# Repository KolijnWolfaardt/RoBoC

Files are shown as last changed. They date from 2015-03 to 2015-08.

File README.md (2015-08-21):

# RoBoC
The RoBoC is a robotics controller board designed for the Robotics club of Stellenbosch. It features a dsPIC33 microcontroller, a motor river and plenty of IO pins. This was designed to be cheaper than off the shelf development boards with the necessary extras.

Please see the full documentation at [http://kolijnwolfaardt.github.io/RoBoC/](http://kolijnwolfaardt.github.io/RoBoC/)

# About the PCB Design
The PCB is designed in [Kicad](www.kicad-pcb.org/). All the project files can be found in *./PCB Design*, and the extra component footprints created are in *./PCB Design/lib*. Some of these components are adapted from the libraries supplied with KiCad. 

The board was originally designed as a 4 layer board, with power and some signals on the inner copper layers. This proved to be too expensive, so the board was redesigned as a 2-layer board.

# Bootloader
## ds30 Bootloader
The ds30 Bootloader code supplied here is a modified version of the [ds30 Loader](http://picbootloader.com/). The following changes were made:

 - The initialization includes configuring the oscillator and PLL
 - The UART initialization was simplified.
 - An LED on the board is turne on and off to indicate when the bootloader is waiting for commands.
 - The memory footprint of the bootloader was reduces by commenting out some of the original (unused) code.

### Compiling the Bootloader
To compile the bootloader the MPLAB IDE v8.92 and the ASM30 compiler were used, on a pc running Windows. The resulting hex file can be written to the board using a PicKit2 or PicKit3.

### Using the Bootloader
To use the bootloader, use the program supplied on the ds30 Loader website.

# Technical Details
 - The Microcontroller is a [dsPic33FJ32GS606](http://www.microchip.com/wwwproducts/Devices.aspx?dDocName=en546851)
 - USB to UART IC is a [MCP2200](http://www.microchip.com/wwwproducts/devices.aspx?dDocName=en546923)
 - The Motor driver is a ON Semiconductor [LV8405V](http://www.onsemi.com/PowerSolutions/product.do?id=LV8405V)
 - The PCB is a 2-layer 5cm by 10cm board

# License
 - The Hardware is licensed under the [CERN OSH License ](http://www.ohwr.org/attachments/2388/cern_ohl_v_1_2.txt)
 - The ds30 Bootloader is licensed under the [GNU GPLv2 Licens](http://www.gnu.org/licenses/old-licenses/gpl-2.0.en.html)
 - Software written for the board is licensed under the [CC Attribution-NonCommerical License ](https://creativecommons.org/licenses/by-nc/2.0/legalcode)

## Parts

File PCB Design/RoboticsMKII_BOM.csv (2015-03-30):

C1 | 1uF | Capacitors_SMD:C_1206
C2 | 100nF | Capacitors_SMD:C_1206
C3 | 1uF | Capacitors_SMD:C_1206
C4 | 1uF | Capacitors_SMD:C_1206
C5 | 100nF | Capacitors_SMD:C_1206
C6 | 100nF | Capacitors_SMD:C_1206
C7 | 100nF | Capacitors_SMD:C_1206
C8 | 100nF | Capacitors_SMD:C_1206
C9 | 100nF | Capacitors_SMD:C_1206
C10 | 10nF | Capacitors_SMD:C_1206
C11 | 100nF | Capacitors_SMD:C_1206
C12 | 10nF | Capacitors_SMD:C_1206
C13 | 10nF | Capacitors_SMD:C_1206
C14 | 10nF | Capacitors_SMD:C_1206
C15 | 22pF | Capacitors_SMD:C_1206
C16 | 22pF | Capacitors_SMD:C_1206
C17 | 100nF | Capacitors_SMD:C_1206
C18 | 22pF | Capacitors_SMD:C_1206
C19 | 22pF | Capacitors_SMD:C_1206
C20 | 10uF | Capacitors_SMD:C_1206
C21 | 100nF | Capacitors_SMD:C_1206
C22 | 10uF | Capacitors_SMD:C_1206
C23 | 1uF | Capacitors_SMD:C_1206
R1 | 220 | Resistors_SMD:R_1206
R2 | 4.7k | Resistors_SMD:R_1206
R3 | 220 | Resistors_SMD:R_1206
R4 | 220 | Resistors_SMD:R_1206
R5 | 220 | Resistors_SMD:R_1206
R6 | 220 | Resistors_SMD:R_1206
R7 | 4.7k | Resistors_SMD:R_1206
R8 | 220 | Resistors_SMD:R_1206
R9 | 4.7k | Resistors_SMD:R_1206
R11 | 220 | Resistors_SMD:R_1206
R12 | 220 | Resistors_SMD:R_1206
R10 | 18k | Resistors_SMD:R_1206
R13 | 220 | Resistors_SMD:R_1206
R14 | 4.7k | Resistors_SMD:R_1206
F1 | FUSE
D1 | LED | LEDs:LED-1206
D2 | LED | LEDs:LED-1206
D3 | LED | LEDs:LED-1206
D4 | LED | LEDs:LED-1206
D5 | LED | LEDs:LED-1206
D6 | LED | LEDs:LED-1206
D7 | LED | LEDs:LED-1206
D8 | LED | LEDs:LED-1206
D9 | D | Diode
RESET1 | DPST | Buttons_Switches_SMD:SW_SPST_PTS645
SW0 | DPST | Buttons_Switches_SMD:SW_SPST_PTS645
SW1 | DPST | Buttons_Switches_SMD:SW_SPST_PTS645
CON1 | USB-MICRO-B | USB
U1 | 3.3VREG
U2 | LV8405V
U3 | MCP2200
U4 | dsPIC33FJ32GS606 | TQFP
X1 | 12MHz
X2 | 10MHz
P1 | CONN_01X03 | Pin_Headers:Pin_Header_Straight_1x03
P2 | CONN_01X02
P3 | CONN_01X03 | Pin_Headers:Pin_Header_Straight_1x03
P4 | CONN_01X03 | Pin_Headers:Pin_Header_Straight_1x03
P5 | CONN_01X03 | Pin_Headers:Pin_Header_Straight_1x03
P6 | CONN_01X03 | Pin_Headers:Pin_Header_Straight_1x03
P7 | CONN_01X03 | Pin_Headers:Pin_Header_Straight_1x03
P8 | CONN_01X03 | Pin_Headers:Pin_Header_Straight_1x03
P9 | CONN_01X08 | Pin_Headers:Pin_Header_Straight_1x08
P10 | CONN_02X11 | Pin_Headers:Pin_Header_Straight_2x11
P11 | CONN_01X03 | Pin_Headers:Pin_Header_Straight_1x03
P12 | CONN_01X02 | Pin_Headers:Pin_Header_Straight_1x02
P13 | CONN_01X06 | Pin_Headers:Pin_Header_Straight_1x06
P14 | CONN_01X06 | Pin_Headers:Pin_Header_Straight_1x06

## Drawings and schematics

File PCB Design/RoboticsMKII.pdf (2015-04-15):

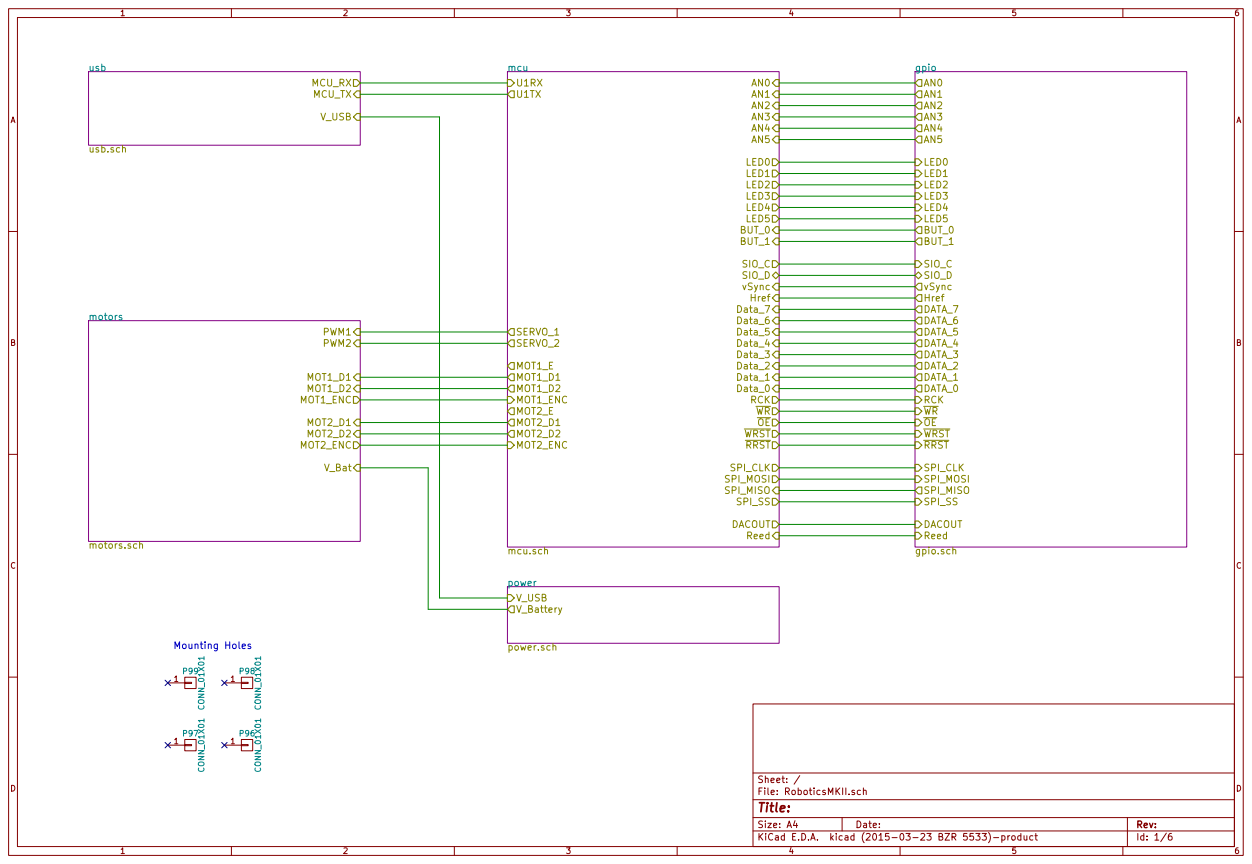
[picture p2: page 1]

Id: 1/6 Title: File: RoboticsMKII.sch Sheet: / power power.sch
V_USB

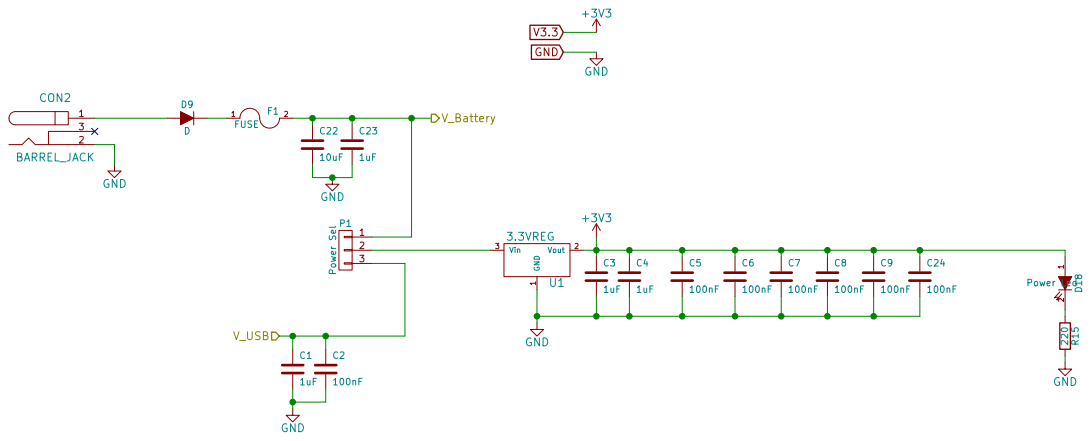
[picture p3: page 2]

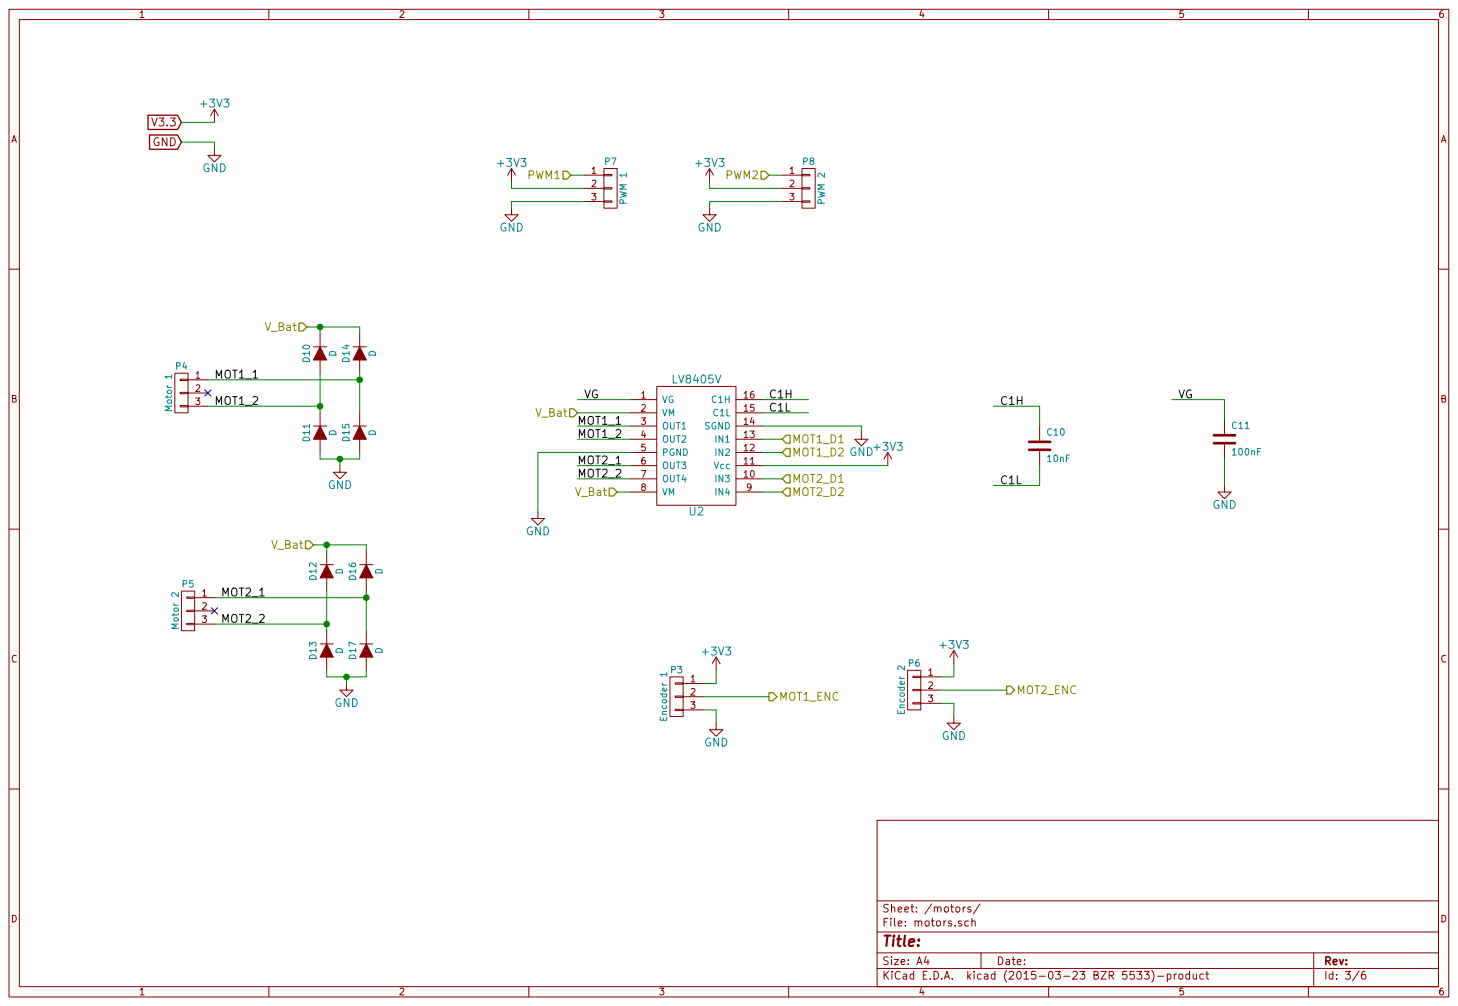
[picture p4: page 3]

Id: 3/6 Title: File: motors.sch Sheet: /motors/

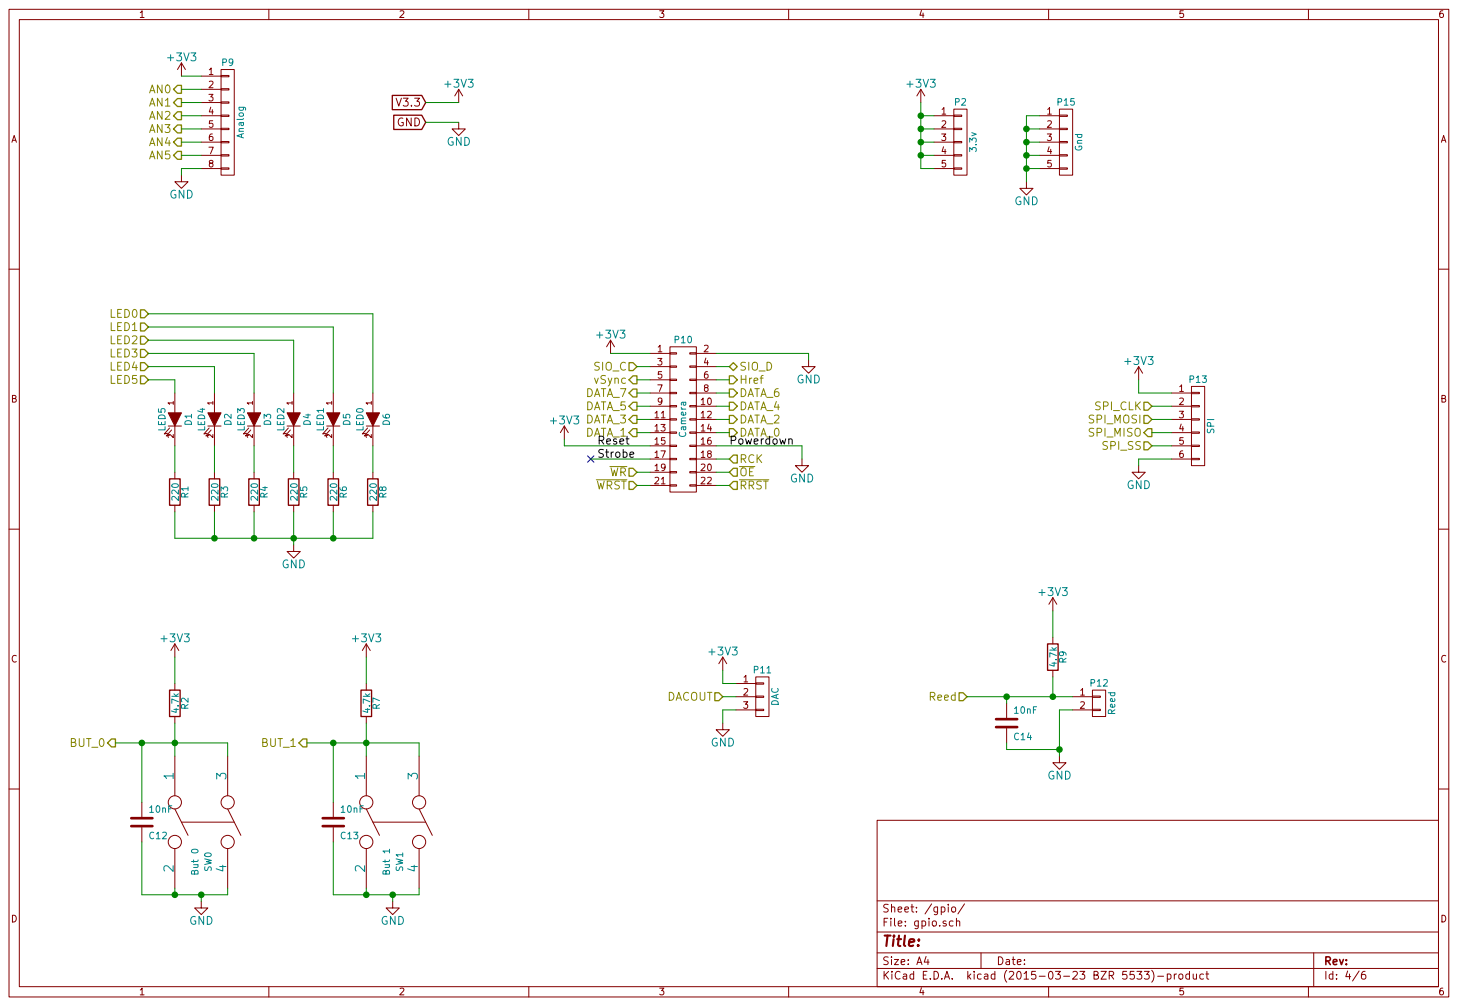
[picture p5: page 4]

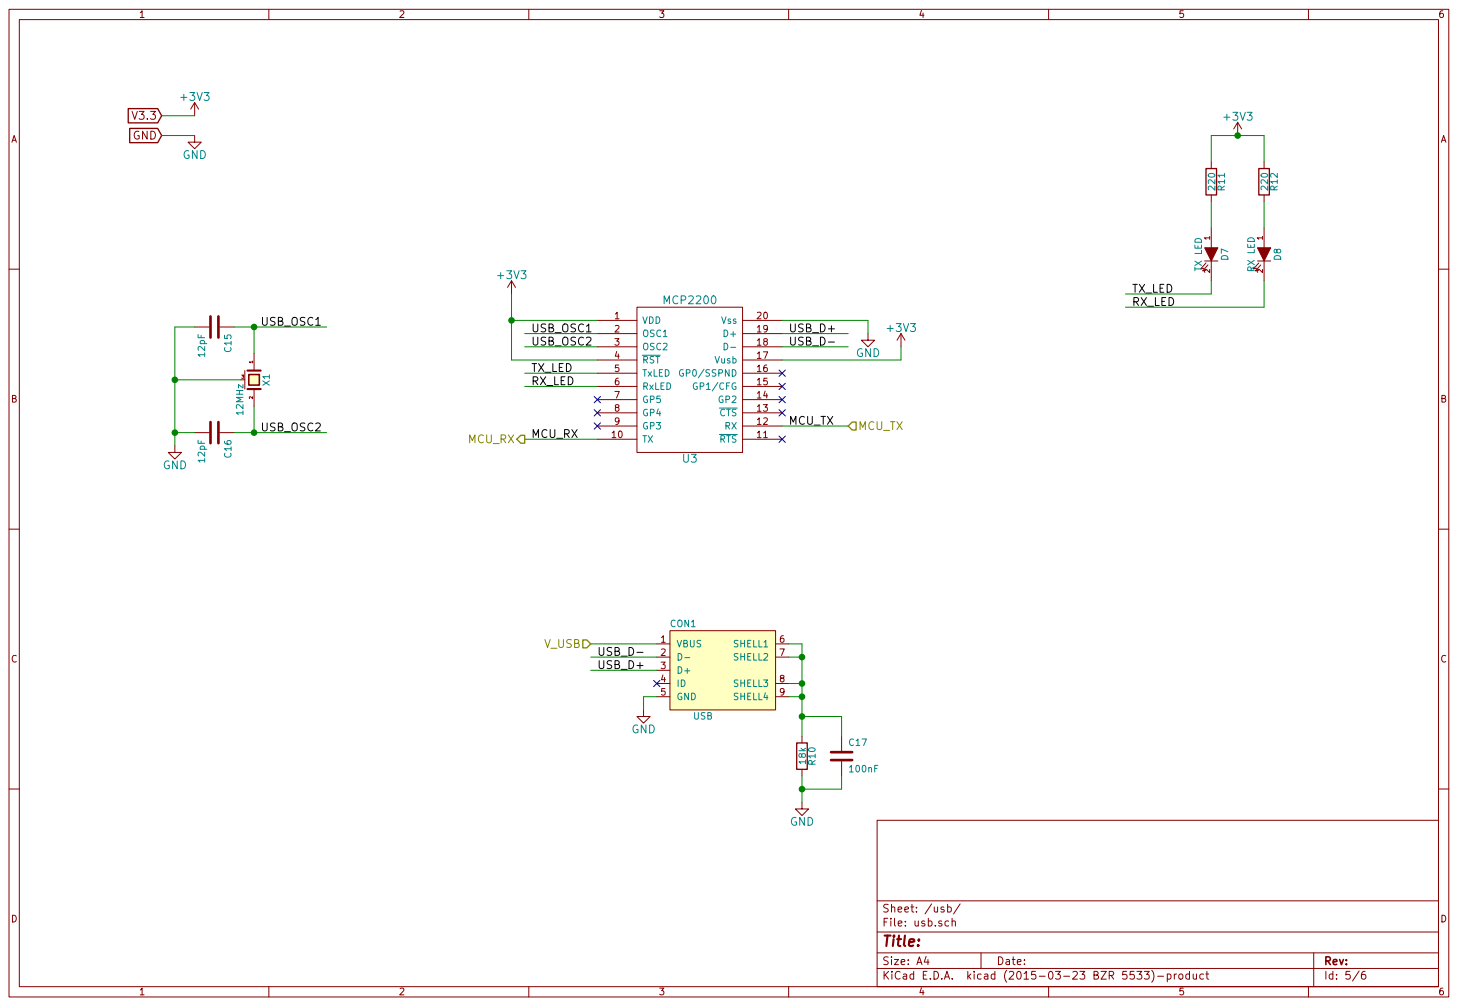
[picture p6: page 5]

Id: 5/6 Title: File: usb.sch Sheet: /usb/

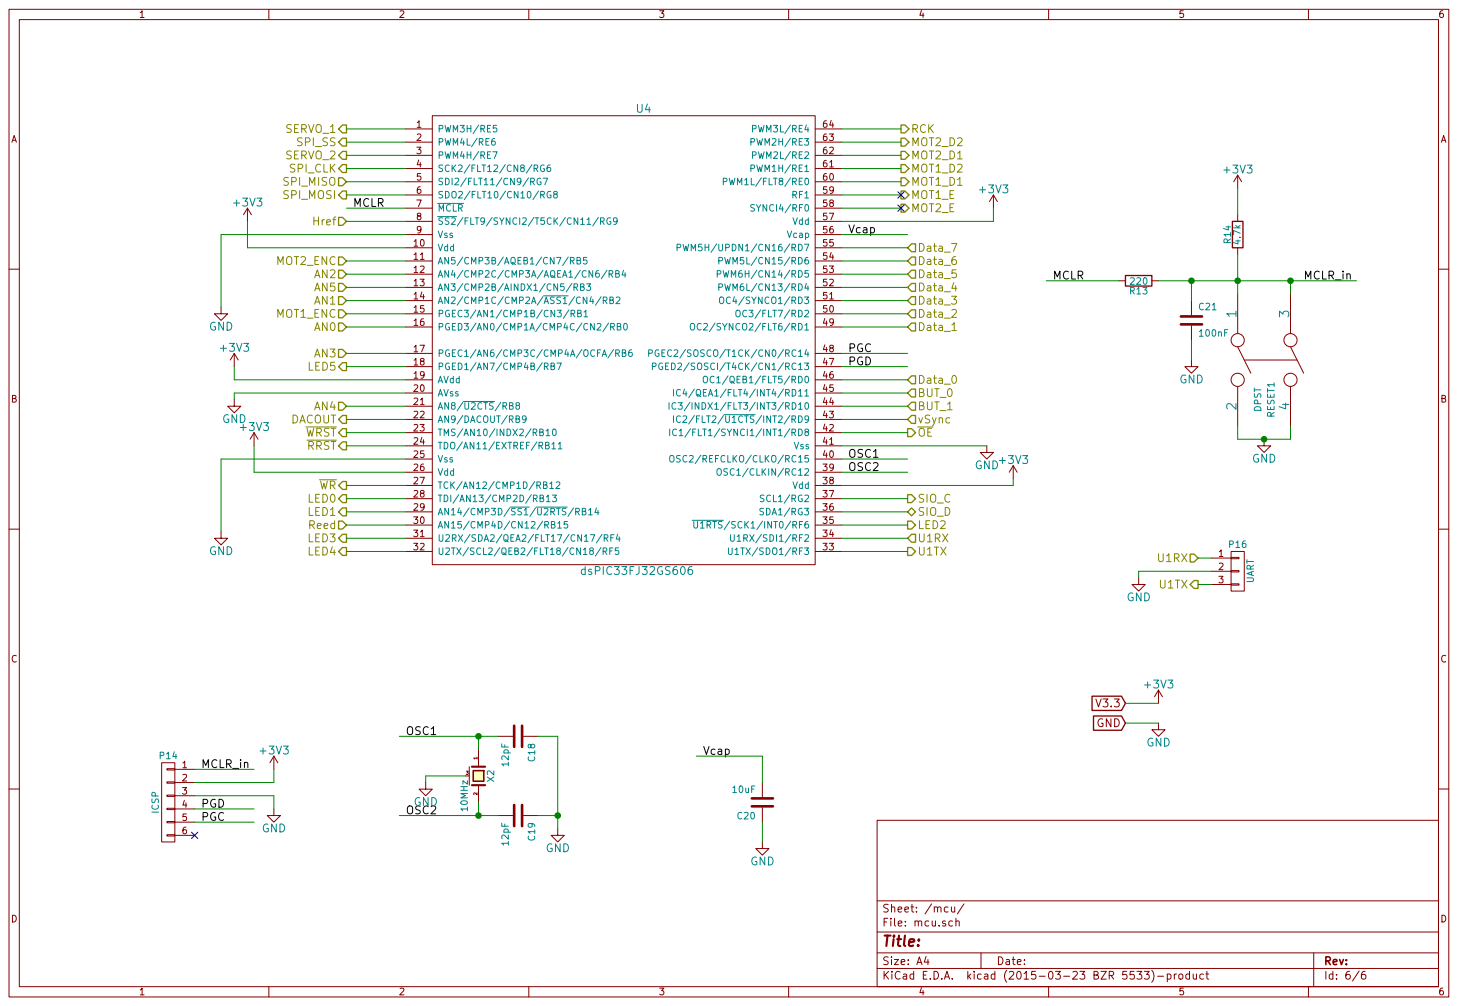
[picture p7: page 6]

Id: 6/6 Title: File: mcu.sch Sheet: /mcu/

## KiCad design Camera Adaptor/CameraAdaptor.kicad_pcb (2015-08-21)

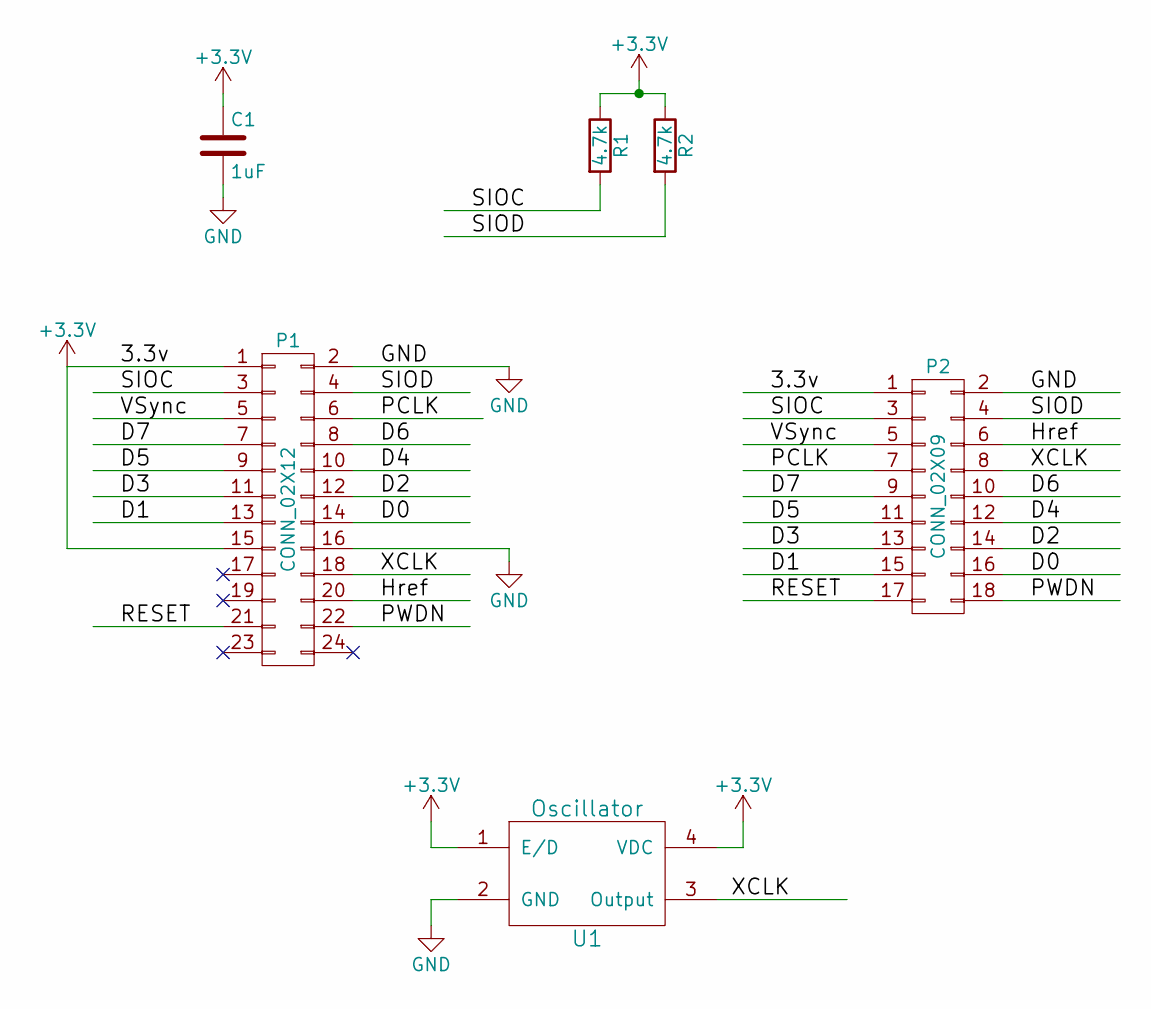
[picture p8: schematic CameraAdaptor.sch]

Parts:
C1: 1uF; C_1206_HandSoldering
P1: CONN_02X12; Pin_Header_Straight_2x12
P2: CONN_02X09; Pin_Header_Straight_2x09
R1, R2: 4.7k; R_1206_HandSoldering
U1: Oscillator; oscillator

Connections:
+3V3: C1.1, P1.1, P1.15, P2.1, R1.1, R2.1, U1.1 (E/D), U1.4 (VDC)
/D0: P1.14, P2.16
/D1: P1.13, P2.15
/D2: P1.12, P2.14
/D3: P1.11, P2.13
/D4: P1.10, P2.12
/D5: P1.9, P2.11
/D6: P1.8, P2.10
/D7: P1.7, P2.9
/Href: P1.20, P2.6
/PCLK: P1.6, P2.7
/PWDN: P1.22, P2.18
/RESET: P1.21, P2.17
/SIOC: P1.3, P2.3, R1.2
/SIOD: P1.4, P2.4, R2.2
/VSync: P1.5, P2.5
/XCLK: P1.18, P2.8, U1.3 (Output)
GND: C1.2, P1.2, P1.16, P2.2, U1.2 (GND)

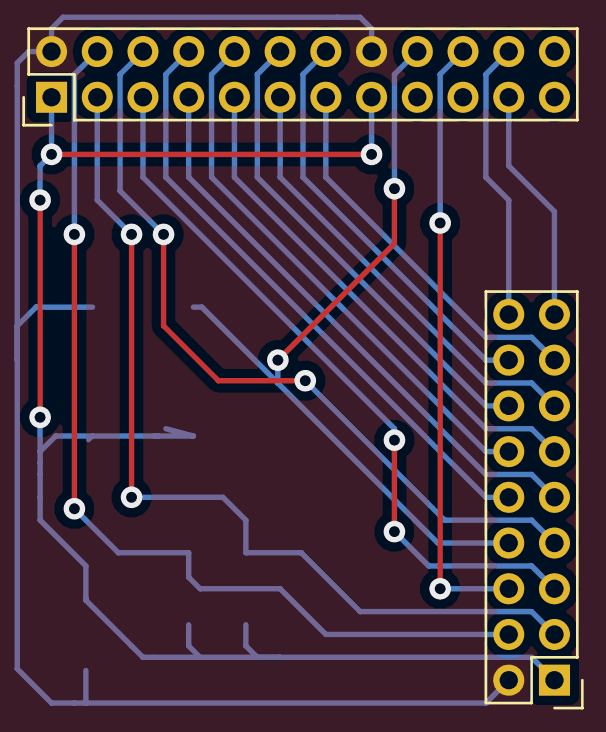
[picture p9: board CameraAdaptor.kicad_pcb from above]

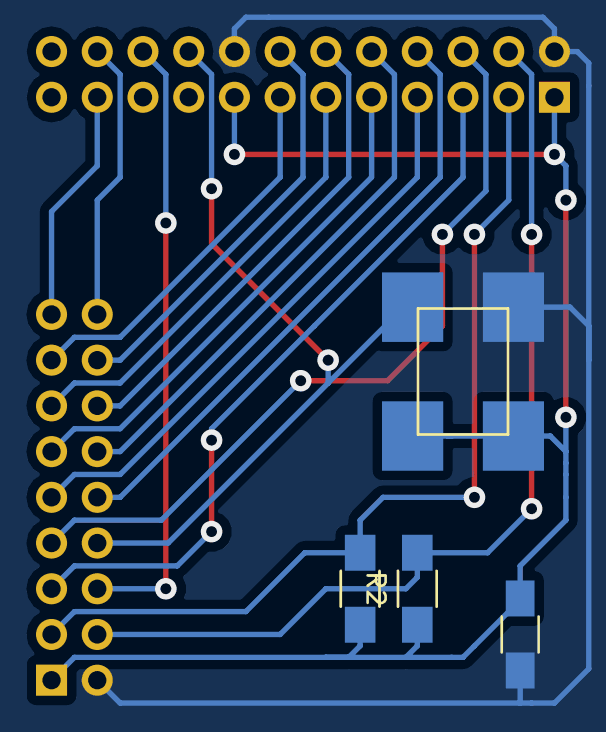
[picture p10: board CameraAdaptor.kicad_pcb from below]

Board: 2 copper layers, 6 parts (4 on the bottom side), 18 nets.

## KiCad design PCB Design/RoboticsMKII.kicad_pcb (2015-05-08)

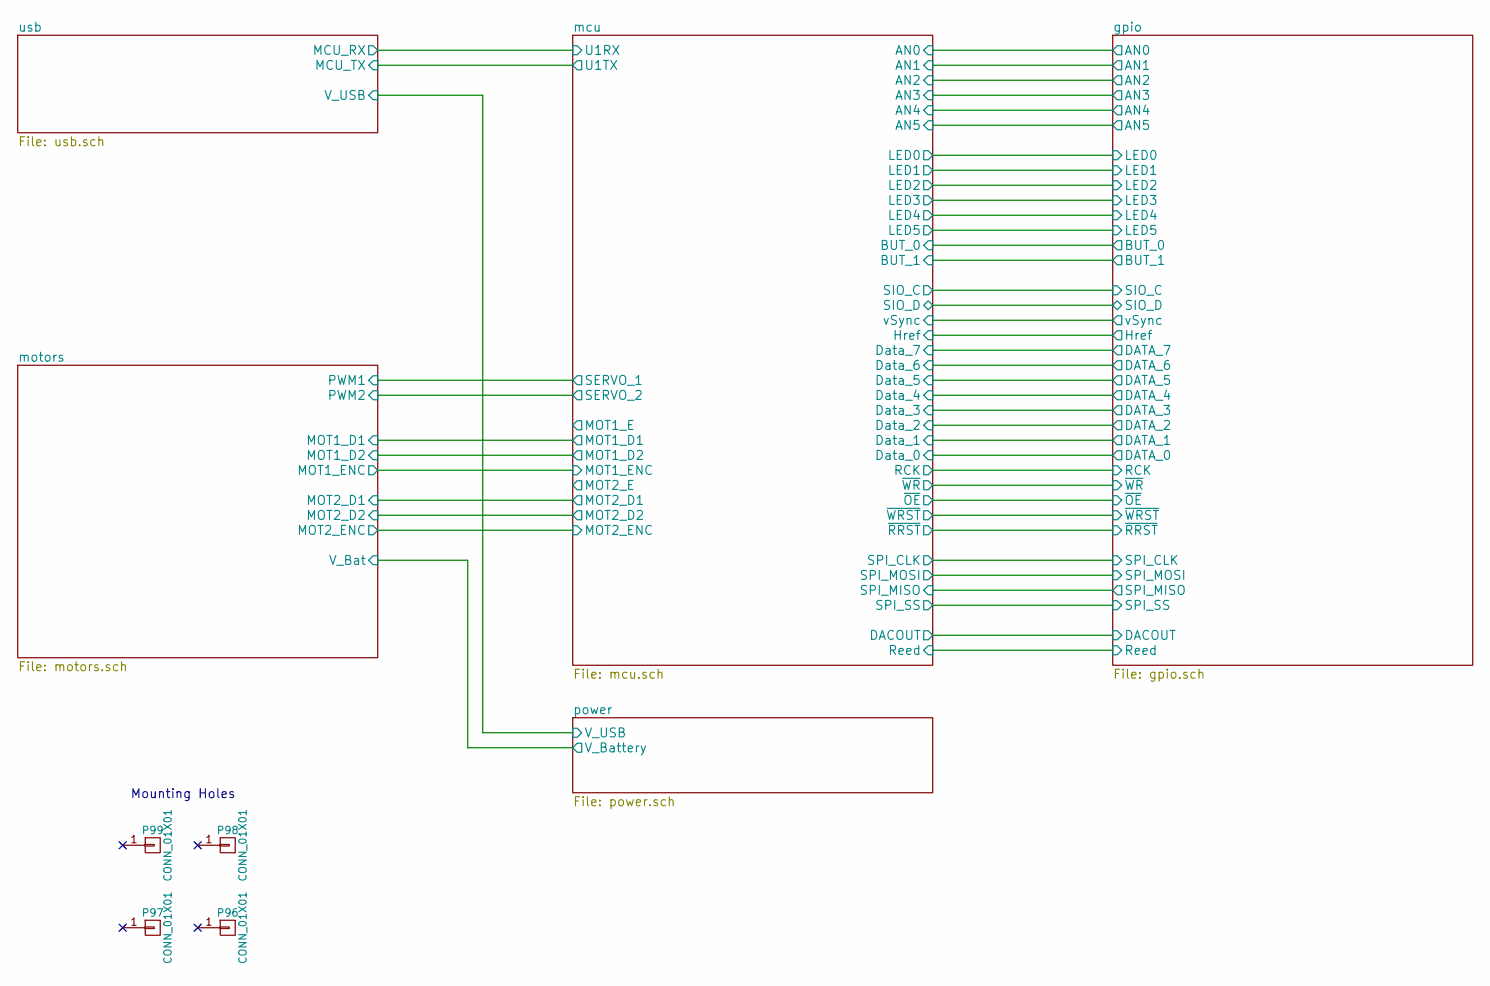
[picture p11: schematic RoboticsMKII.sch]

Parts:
P96, P97, P98, P99: CONN_01X01; MountingHole3mm

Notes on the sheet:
Mounting Holes

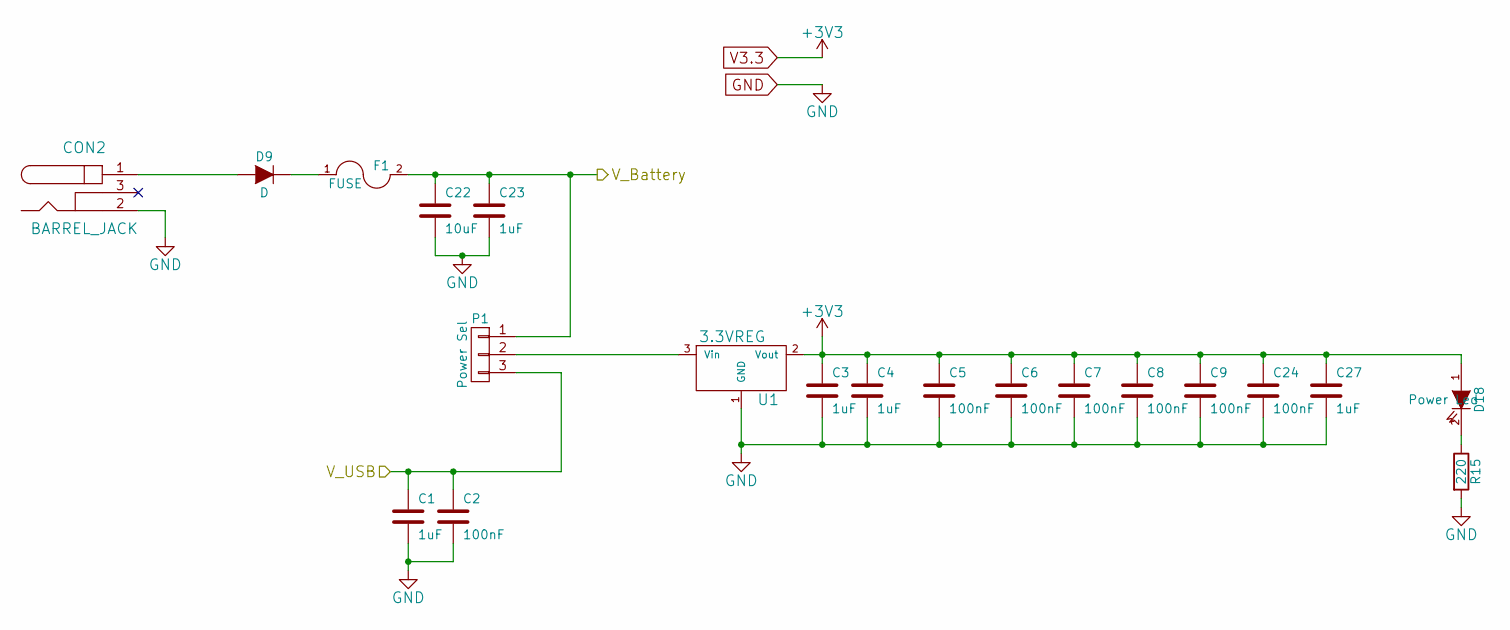
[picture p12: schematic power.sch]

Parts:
C1, C3, C4, C23, C27: 1uF; C_1206
C2, C5, C6, C7, C8, C9, C24: 100nF; C_1206
C22: 10uF; C_1206
CON2: BARREL_JACK
D9: D; Diode-SMC_Handsoldering
D18: Power Led; LED-1206
F1: FUSE; R_1206_HandSoldering
P1: Power Sel; Pin_Header_Straight_1x03
R15: 220; R_1206
U1: 3.3VREG; SOT-223

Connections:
/motors/V_Bat: C22.1, C23.1, F1.2, P1.1; also elsewhere on the board
/power/V_USB: C1.1, C2.1, P1.3; also elsewhere on the board
GND: C1.2, C2.2, C3.2, C4.2, C5.2, C6.2, C7.2, C8.2, C9.2, C22.2, C23.2, C24.2, C27.2, CON2.2, R15.2, U1.1 (GND); also elsewhere on the board
unnamed: CON2.1, D9.1 (A)
unnamed: D9.2 (K), F1.1
unnamed: D18.2 (K), R15.1
unnamed: P1.2, U1.3 (Vin)
V3.3: C3.1, C4.1, C5.1, C6.1, C7.1, C8.1, C9.1, C24.1, C27.1, D18.1 (A), U1.2 (Vout); also elsewhere on the board

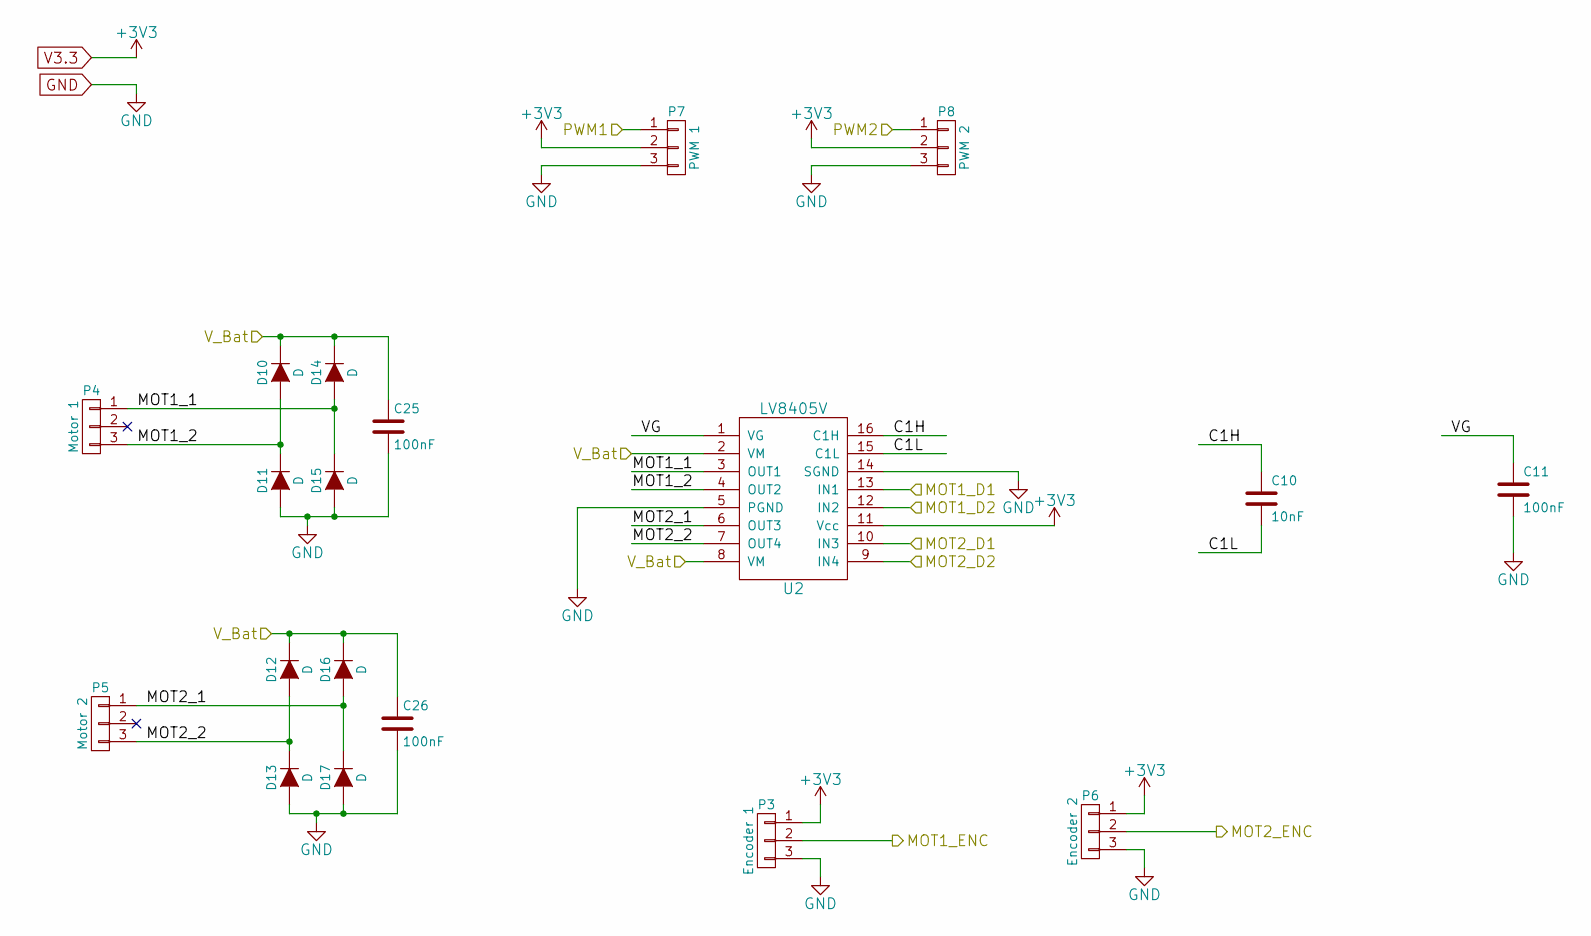
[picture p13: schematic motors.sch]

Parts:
C10: 10nF; C_1206
C11, C25, C26: 100nF; C_1206
D10, D11, D12, D13, D14, D15, D16, D17: D; SOD-323
P3: Encoder 1; Pin_Header_Straight_1x03
P4: Motor 1; Pin_Header_Straight_1x03
P5: Motor 2; Pin_Header_Straight_1x03
P6: Encoder 2; Pin_Header_Straight_1x03
P7: PWM 1; Pin_Header_Straight_1x03
P8: PWM 2; Pin_Header_Straight_1x03
U2: LV8405V; SSOP-16_4.4x5.2mm_Pitch0.65mm_Handsoldering

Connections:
/mcu/MOT1_D1: U2.13 (IN1); also elsewhere on the board
/mcu/MOT1_D2: U2.12 (IN2); also elsewhere on the board
/mcu/MOT1_ENC: P3.2; also elsewhere on the board
/mcu/MOT2_D1: U2.10 (IN3); also elsewhere on the board
/mcu/MOT2_D2: U2.9 (IN4); also elsewhere on the board
/mcu/MOT2_ENC: P6.2; also elsewhere on the board
/motors/C1H: C10.1, U2.16 (C1H)
/motors/C1L: C10.2, U2.15 (C1L)
/motors/MOT1_1: D14.1 (A), D15.2 (K), P4.1, U2.3 (OUT1)
/motors/MOT1_2: D10.1 (A), D11.2 (K), P4.3, U2.4 (OUT2)
/motors/MOT2_1: D16.1 (A), D17.2 (K), P5.1, U2.6 (OUT3)
/motors/MOT2_2: D12.1 (A), D13.2 (K), P5.3, U2.7 (OUT4)
/motors/PWM1: P7.1; also elsewhere on the board
/motors/PWM2: P8.1; also elsewhere on the board
/motors/VG: C11.1, U2.1 (VG)
/motors/V_Bat: C25.1, C26.1, D10.2 (K), D12.2 (K), D14.2 (K), D16.2 (K), U2.2 (VM), U2.8 (VM); also elsewhere on the board
GND: C11.2, C25.2, C26.2, D11.1 (A), D13.1 (A), D15.1 (A), D17.1 (A), P3.3, P6.3, P7.3, P8.3, U2.5 (PGND), U2.14 (SGND); also elsewhere on the board
V3.3: P3.1, P6.1, P7.2, P8.2, U2.11 (Vcc); also elsewhere on the board

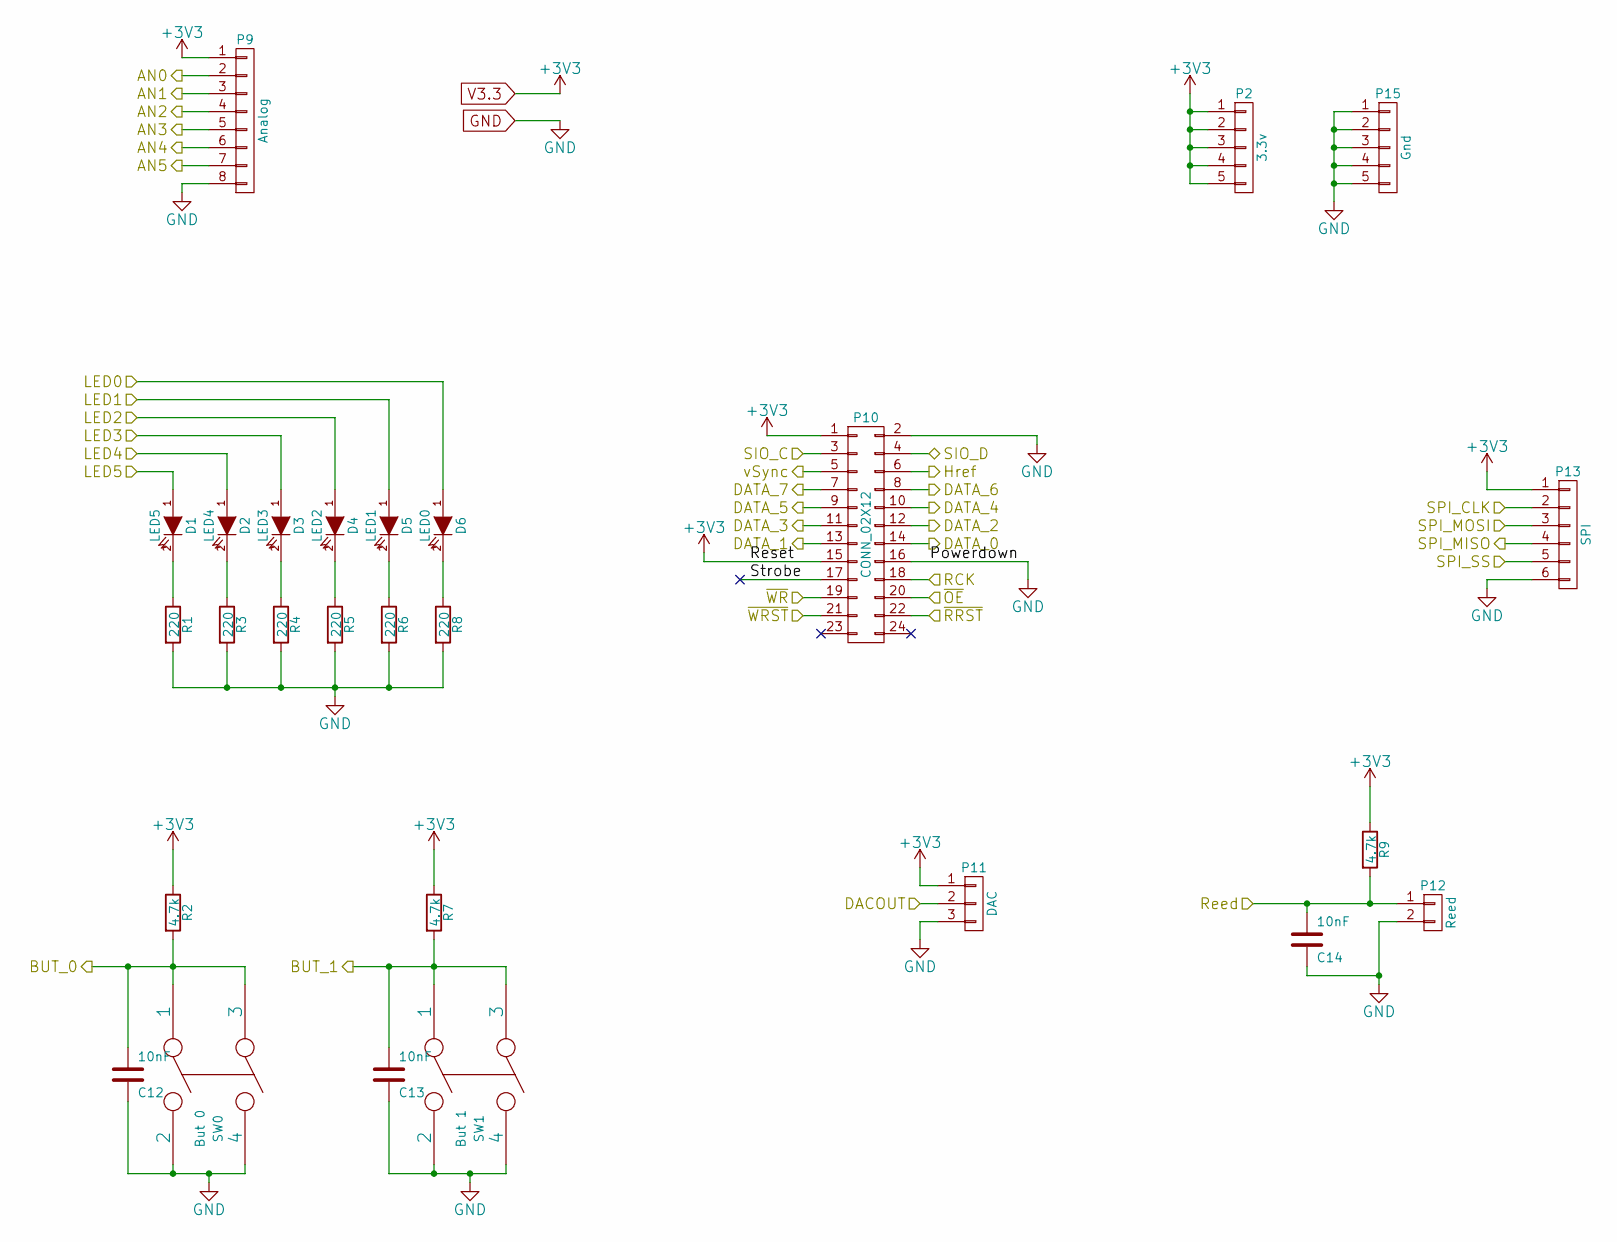
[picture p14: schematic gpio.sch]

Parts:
C12, C13, C14: 10nF; C_1206
D1: LED5; LED-1206
D2: LED4; LED-1206
D3: LED3; LED-1206
D4: LED2; LED-1206
D5: LED1; LED-1206
D6: LED0; LED-1206
P2: 3.3v; Pin_Header_Straight_1x05
P9: Analog; Pin_Header_Straight_1x08
P10: CONN_02X12; Pin_Header_Straight_2x12
P11: DAC; Pin_Header_Straight_1x03
P12: Reed; Pin_Header_Straight_1x02
P13: SPI; Pin_Header_Straight_1x06
P15: Gnd; Pin_Header_Straight_1x05
R1, R3, R4, R5, R6, R8: 220; R_1206
R2, R7, R9: 4.7k; R_1206
SW0: But 0; SW_SPST_bigpads
SW1: But 1; SW_SPST_bigpads

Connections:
/gpio/AN0: P9.2; also elsewhere on the board
/gpio/AN1: P9.3; also elsewhere on the board
/gpio/AN2: P9.4; also elsewhere on the board
/gpio/AN3: P9.5; also elsewhere on the board
/gpio/AN4: P9.6; also elsewhere on the board
/gpio/AN5: P9.7; also elsewhere on the board
/gpio/BUT_0: C12.2, R2.2, SW0.1, SW0.3; also elsewhere on the board
/gpio/BUT_1: C13.2, R7.2, SW1.1, SW1.3; also elsewhere on the board
/gpio/DACOUT: P11.2; also elsewhere on the board
/gpio/DATA_0: P10.14; also elsewhere on the board
/gpio/DATA_1: P10.13; also elsewhere on the board
/gpio/DATA_2: P10.12; also elsewhere on the board
/gpio/DATA_3: P10.11; also elsewhere on the board
/gpio/DATA_4: P10.10; also elsewhere on the board
/gpio/DATA_5: P10.9; also elsewhere on the board
/gpio/DATA_6: P10.8; also elsewhere on the board
/gpio/DATA_7: P10.7; also elsewhere on the board
/gpio/Href: P10.6; also elsewhere on the board
/gpio/LED0: D6.1 (A); also elsewhere on the board
/gpio/LED1: D5.1 (A); also elsewhere on the board
/gpio/LED2: D4.1 (A); also elsewhere on the board
/gpio/LED3: D3.1 (A); also elsewhere on the board
/gpio/LED4: D2.1 (A); also elsewhere on the board
/gpio/LED5: D1.1 (A); also elsewhere on the board
/gpio/RCK: P10.18; also elsewhere on the board
/gpio/Reed: C14.2, P12.1, R9.2; also elsewhere on the board
/gpio/SIO_C: P10.3; also elsewhere on the board
/gpio/SIO_D: P10.4; also elsewhere on the board
/gpio/SPI_CLK: P13.2; also elsewhere on the board
/gpio/SPI_MISO: P13.4; also elsewhere on the board
/gpio/SPI_MOSI: P13.3; also elsewhere on the board
/gpio/SPI_SS: P13.5; also elsewhere on the board
/gpio/Strobe: P10.17
/gpio/vSync: P10.5; also elsewhere on the board
/gpio/~OE: P10.20; also elsewhere on the board
/gpio/~RRST: P10.22; also elsewhere on the board
/gpio/~WR: P10.19; also elsewhere on the board
/gpio/~WRST: P10.21; also elsewhere on the board
GND: C12.1, C13.1, C14.1, P9.8, P10.2, P10.16, P11.3, P12.2, P13.6, P15.1, P15.2, P15.3, P15.4, P15.5, R1.2, R3.2, R4.2, R5.2, R6.2, R8.2, SW0.2, SW0.4, SW1.2, SW1.4; also elsewhere on the board
unnamed: D1.2 (K), R1.1
unnamed: D2.2 (K), R3.1
unnamed: D3.2 (K), R4.1
unnamed: D4.2 (K), R5.1
unnamed: D5.2 (K), R6.1
unnamed: D6.2 (K), R8.1
V3.3: P2.1, P2.2, P2.3, P2.4, P2.5, P9.1, P10.1, P10.15, P11.1, P13.1, R2.1, R7.1, R9.1; also elsewhere on the board

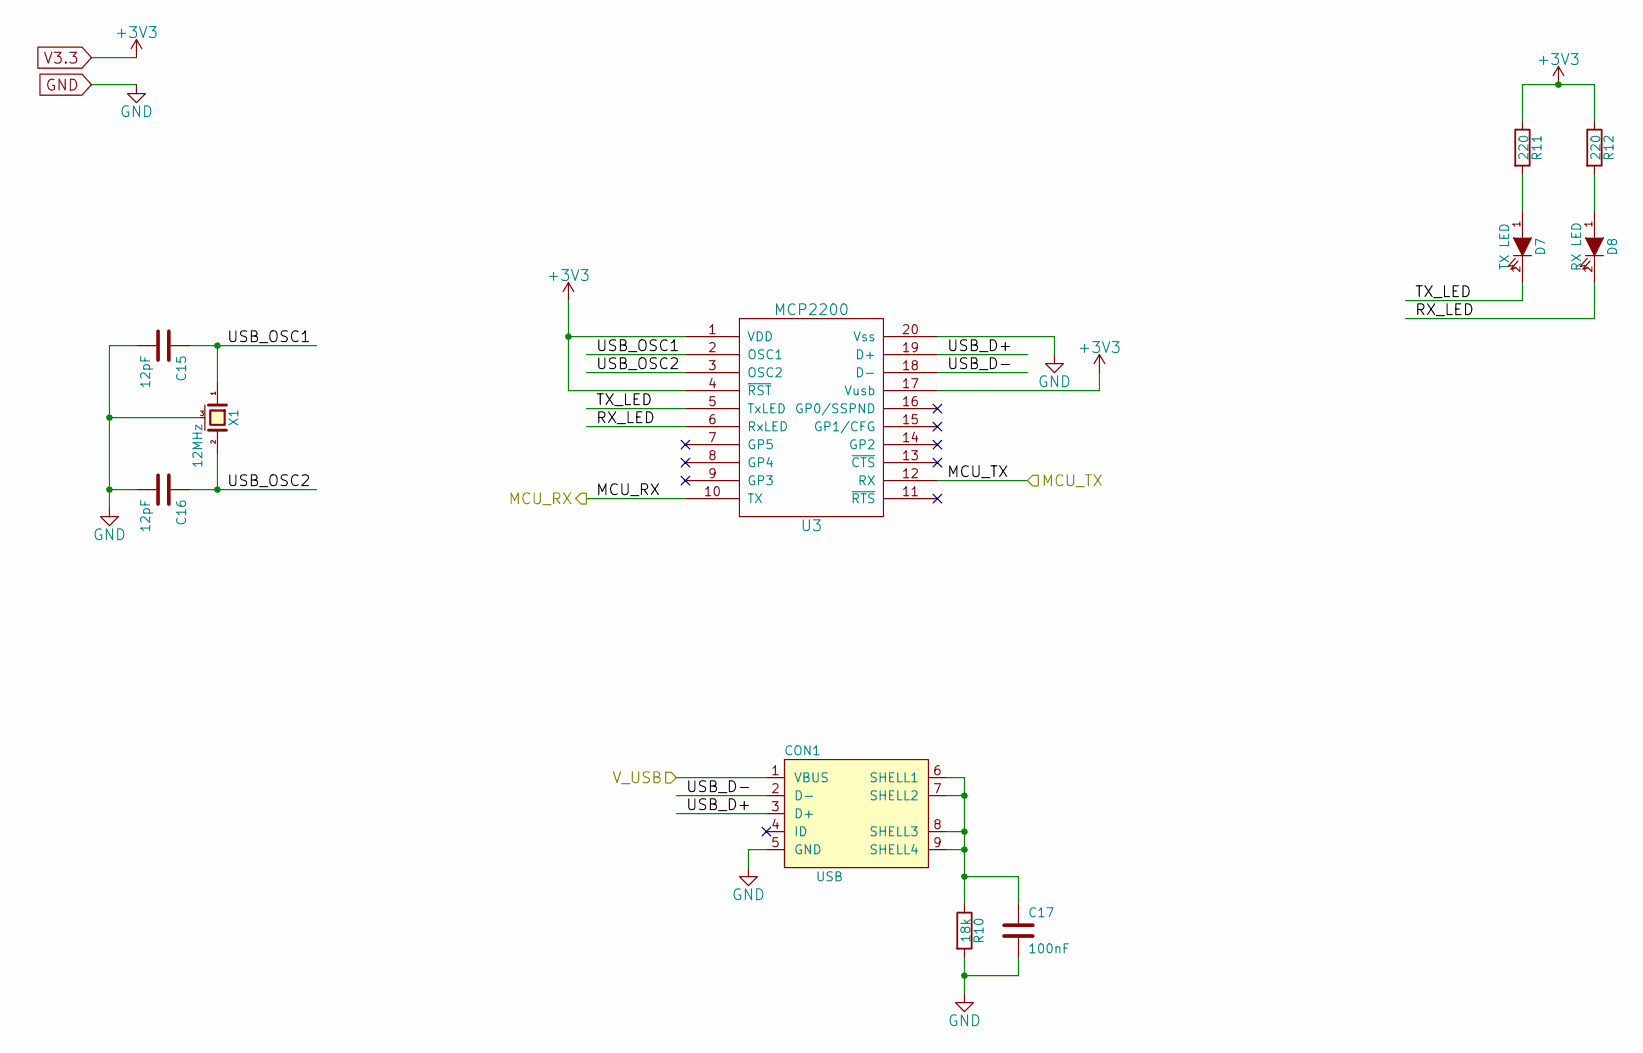
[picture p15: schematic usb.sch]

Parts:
C15, C16: 12pF; C_1206
C17: 100nF; C_1206
CON1: USB; USB_Micro
D7: TX LED; LED-1206
D8: RX LED; LED-1206
R10: 18k; R_1206
R11, R12: 220; R_1206
U3: MCP2200; SOIC-20_7.5x12.8mm_Pitch1.27mm
X1: 12MHz; Crystal 6x 3.5 x 1.1mm

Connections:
/power/V_USB: CON1.1 (VBUS); also elsewhere on the board
/usb/MCU_RX: U3.10 (TX); also elsewhere on the board
/usb/MCU_TX: U3.12 (RX); also elsewhere on the board
/usb/RX_LED: D8.2 (K), U3.6 (RxLED)
/usb/TX_LED: D7.2 (K), U3.5 (TxLED)
/usb/USB_D+: CON1.3 (D+), U3.19 (D+)
/usb/USB_D-: CON1.2 (D-), U3.18 (D-)
/usb/USB_OSC1: C15.1, U3.2 (OSC1), X1.1
/usb/USB_OSC2: C16.1, U3.3 (OSC2), X1.2
GND: C15.2, C16.2, C17.2, CON1.5 (GND), R10.2, U3.20 (Vss), X1.3 (case); also elsewhere on the board
unnamed: C17.1, CON1.6 (SHELL1), CON1.7 (SHELL2), CON1.8 (SHELL3), CON1.9 (SHELL4), R10.1
unnamed: D7.1 (A), R11.2
unnamed: D8.1 (A), R12.2
V3.3: R11.1, R12.1, U3.1 (VDD), U3.4 (~RST), U3.17 (Vusb); also elsewhere on the board

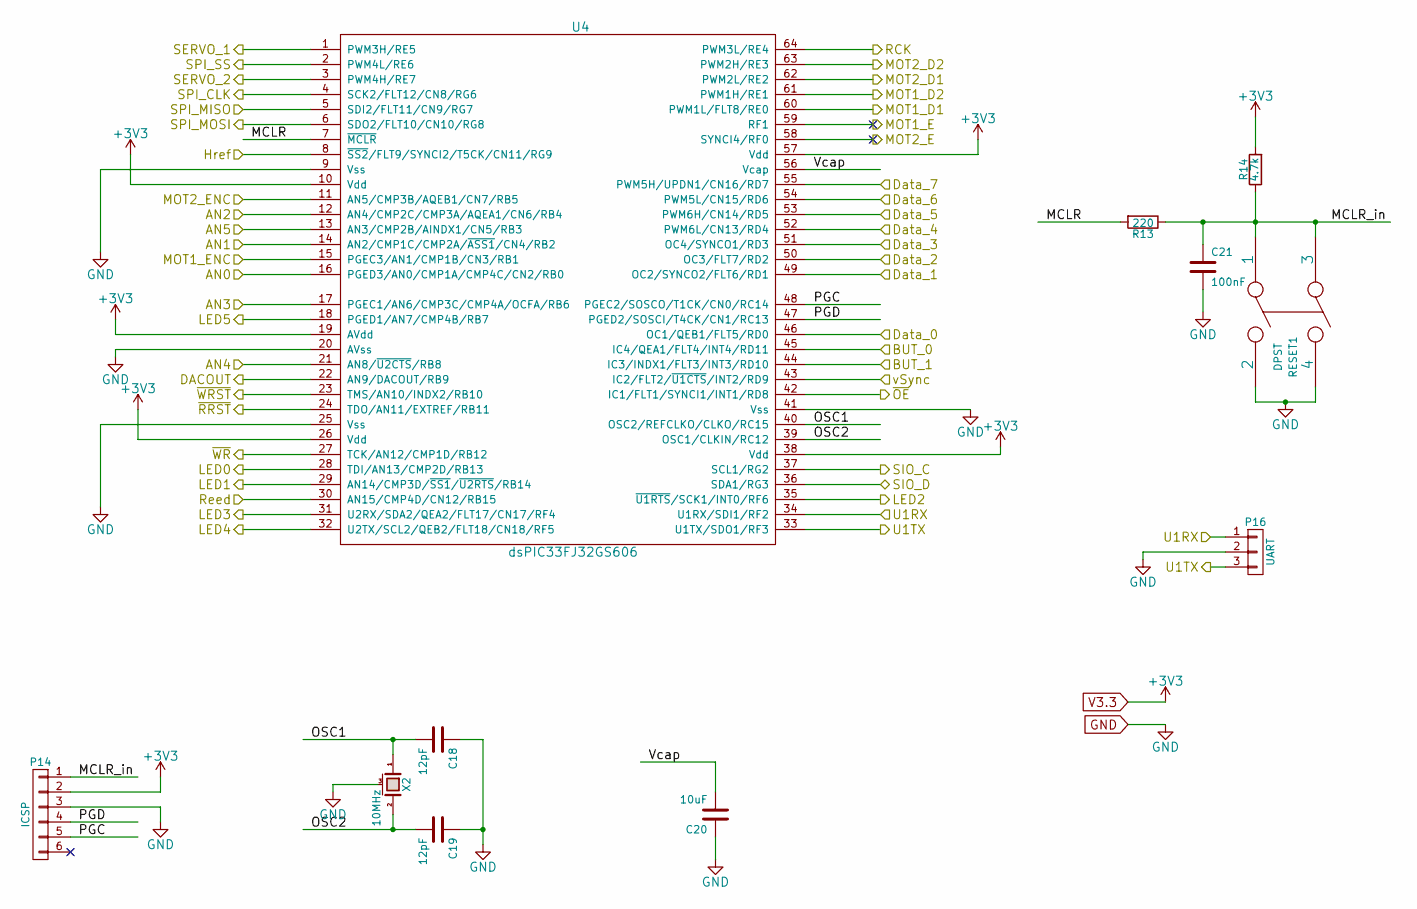
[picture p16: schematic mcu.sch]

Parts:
C18, C19: 12pF; C_1206
C20: 10uF; C_1206
C21: 100nF; C_1206
P14: ICSP; Pin_Header_Straight_1x06
P16: UART; Pin_Header_Straight_1x03
R13: 220; R_1206
R14: 4.7k; R_1206
RESET1: DPST; SW_SPST_bigpads
U4: dsPIC33FJ32GS606; TQFP-64_10x10mm_Pitch0.5mm_handsoldering
X2: 10MHz; Crystal 6x 3.5 x 1.1mm

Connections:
/gpio/AN0: U4.16 (PGED3/AN0/CMP1A/CMP4C/CN2/RB0); also elsewhere on the board
/gpio/AN1: U4.14 (AN2/CMP1C/CMP2A/~ASS1~/CN4/RB2); also elsewhere on the board
/gpio/AN2: U4.12 (AN4/CMP2C/CMP3A/AQEA1/CN6/RB4); also elsewhere on the board
/gpio/AN3: U4.17 (PGEC1/AN6/CMP3C/CMP4A/OCFA/RB6); also elsewhere on the board
/gpio/AN4: U4.21 (AN8/~U2CTS~/RB8); also elsewhere on the board
/gpio/AN5: U4.13 (AN3/CMP2B/AINDX1/CN5/RB3); also elsewhere on the board
/gpio/BUT_0: U4.45 (IC4/QEA1/FLT4/INT4/RD11); also elsewhere on the board
/gpio/BUT_1: U4.44 (IC3/INDX1/FLT3/INT3/RD10); also elsewhere on the board
/gpio/DACOUT: U4.22 (AN9/DACOUT/RB9); also elsewhere on the board
/gpio/DATA_0: U4.46 (OC1/QEB1/FLT5/RD0); also elsewhere on the board
/gpio/DATA_1: U4.49 (OC2/SYNCO2/FLT6/RD1); also elsewhere on the board
/gpio/DATA_2: U4.50 (OC3/FLT7/RD2); also elsewhere on the board
/gpio/DATA_3: U4.51 (OC4/SYNCO1/RD3); also elsewhere on the board
/gpio/DATA_4: U4.52 (PWM6L/CN13/RD4); also elsewhere on the board
/gpio/DATA_5: U4.53 (PWM6H/CN14/RD5); also elsewhere on the board
/gpio/DATA_6: U4.54 (PWM5L/CN15/RD6); also elsewhere on the board
/gpio/DATA_7: U4.55 (PWM5H/UPDN1/CN16/RD7); also elsewhere on the board
/gpio/Href: U4.8 (~SS2~/FLT9/SYNCI2/T5CK/CN11/RG9); also elsewhere on the board
/gpio/LED0: U4.28 (TDI/AN13/CMP2D/RB13); also elsewhere on the board
/gpio/LED1: U4.29 (AN14/CMP3D/~SS1~/~U2RTS~/RB14); also elsewhere on the board
/gpio/LED2: U4.35 (~U1RTS~/SCK1/INT0/RF6); also elsewhere on the board
/gpio/LED3: U4.31 (U2RX/SDA2/QEA2/FLT17/CN17/RF4); also elsewhere on the board
/gpio/LED4: U4.32 (U2TX/SCL2/QEB2/FLT18/CN18/RF5); also elsewhere on the board
/gpio/LED5: U4.18 (PGED1/AN7/CMP4B/RB7); also elsewhere on the board
/gpio/RCK: U4.64 (PWM3L/RE4); also elsewhere on the board
/gpio/Reed: U4.30 (AN15/CMP4D/CN12/RB15); also elsewhere on the board
/gpio/SIO_C: U4.37 (SCL1/RG2); also elsewhere on the board
/gpio/SIO_D: U4.36 (SDA1/RG3); also elsewhere on the board
/gpio/SPI_CLK: U4.4 (SCK2/FLT12/CN8/RG6); also elsewhere on the board
/gpio/SPI_MISO: U4.5 (SDI2/FLT11/CN9/RG7); also elsewhere on the board
/gpio/SPI_MOSI: U4.6 (SDO2/FLT10/CN10/RG8); also elsewhere on the board
/gpio/SPI_SS: U4.2 (PWM4L/RE6); also elsewhere on the board
/gpio/vSync: U4.43 (IC2/FLT2/~U1CTS~/INT2/RD9); also elsewhere on the board
/gpio/~OE: U4.42 (IC1/FLT1/SYNCI1/INT1/RD8); also elsewhere on the board
/gpio/~RRST: U4.24 (TDO/AN11/EXTREF/RB11); also elsewhere on the board
/gpio/~WR: U4.27 (TCK/AN12/CMP1D/RB12); also elsewhere on the board
/gpio/~WRST: U4.23 (TMS/AN10/INDX2/RB10); also elsewhere on the board
/mcu/MCLR: R13.2, U4.7 (~MCLR~)
/mcu/MCLR_in: C21.1, P14.1, R13.1, R14.1, RESET1.1, RESET1.3
/mcu/MOT1_D1: U4.60 (PWM1L/FLT8/RE0); also elsewhere on the board
/mcu/MOT1_D2: U4.61 (PWM1H/RE1); also elsewhere on the board
/mcu/MOT1_E: U4.59 (RF1)
/mcu/MOT1_ENC: U4.15 (PGEC3/AN1/CMP1B/CN3/RB1); also elsewhere on the board
/mcu/MOT2_D1: U4.62 (PWM2L/RE2); also elsewhere on the board
/mcu/MOT2_D2: U4.63 (PWM2H/RE3); also elsewhere on the board
/mcu/MOT2_E: U4.58 (SYNCI4/RF0)
/mcu/MOT2_ENC: U4.11 (AN5/CMP3B/AQEB1/CN7/RB5); also elsewhere on the board
/mcu/OSC1: C18.2, U4.40 (OSC2/REFCLKO/CLKO/RC15), X2.1
/mcu/OSC2: C19.2, U4.39 (OSC1/CLKIN/RC12), X2.2
/mcu/PGC: P14.5, U4.48 (PGEC2/SOSCO/T1CK/CN0/RC14)
/mcu/PGD: P14.4, U4.47 (PGED2/SOSCI/T4CK/CN1/RC13)
/mcu/Vcap: C20.2, U4.56 (Vcap)
/motors/PWM1: U4.1 (PWM3H/RE5); also elsewhere on the board
/motors/PWM2: U4.3 (PWM4H/RE7); also elsewhere on the board
/usb/MCU_RX: P16.1, U4.34 (U1RX/SDI1/RF2); also elsewhere on the board
/usb/MCU_TX: P16.3, U4.33 (U1TX/SDO1/RF3); also elsewhere on the board
GND: C18.1, C19.1, C20.1, C21.2, P14.3, P16.2, RESET1.2, RESET1.4, U4.9 (Vss), U4.20 (AVss), U4.25 (Vss), U4.41 (Vss), X2.3 (case); also elsewhere on the board
V3.3: P14.2, R14.2, U4.10 (Vdd), U4.19 (AVdd), U4.26 (Vdd), U4.38 (Vdd), U4.57 (Vdd); also elsewhere on the board

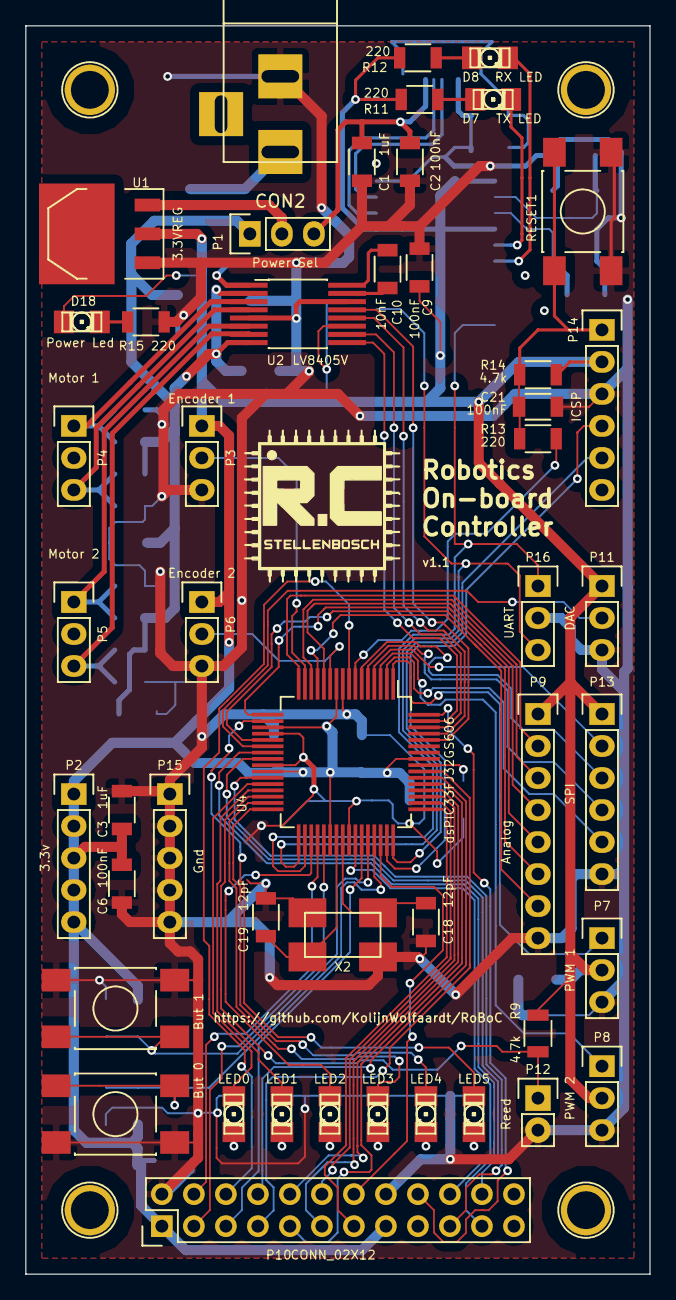
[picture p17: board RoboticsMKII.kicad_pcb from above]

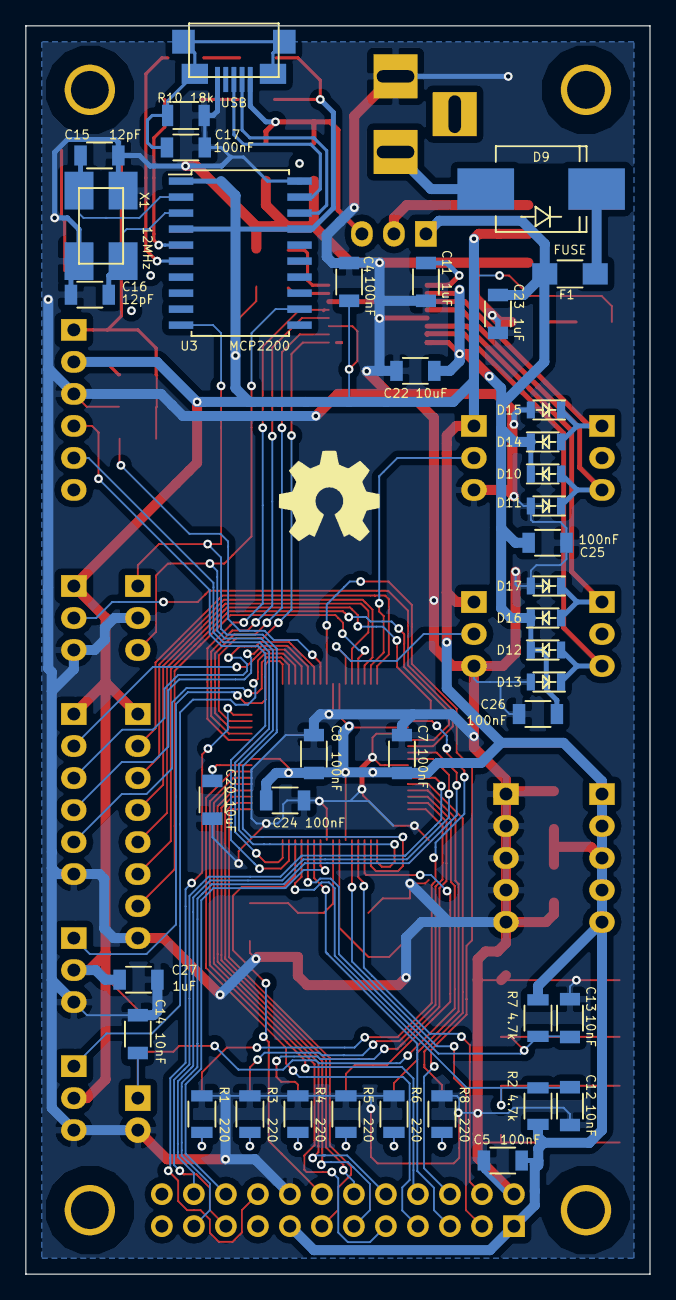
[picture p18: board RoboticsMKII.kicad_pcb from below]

Board: 2 copper layers, 49.5 x 99.1 mm, 92 parts (40 on the bottom side), 84 nets.

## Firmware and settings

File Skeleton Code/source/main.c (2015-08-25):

#include <stdlib.h>
#include <xc.h>

#include "hardware_config.h"
#include "adc.h"
#include "camera.h"
#include "gpio.h"
#include "servo.h"
#include "timer.h"
#include "uart.h"





/* =========================================================
 *              Function Prototypes
 * ====================================================== */

/* =========================================================
 *              Global Variables
 * ====================================================== */
int but0_down = 0;
int but1_down = 0;
int led_number = 0;

/* =========================================================
 *              Interrupt Service Routines
 * ====================================================== */



/* =========================================================
 *              Main function
 * ====================================================== */
int main(int argc, char** argv)
{
    configure_oscillator();
    setup_gpio(); 
    setup_uart();
    setup_pwm();
    setup_adc();
    setup_timer_1();
    setup_camera(); 
    
    // Uncomment to enable the ADC
    //adc_enable();
    
    //THis is for camera debugging
    //Use the SPI_SS pin as an output
    TRISEbits.TRISE6 = 0; 
    //Use the SPI_miso pin as an ouput
    TRISGbits.TRISG7 = 0;
   
    while(1)
    {
        //Check for button 0
        if (but0_down == 0)
        {
            if (BUT0 == 0)
            {
                led_number++;
                led_write(led_number);
                
                but0_down = 1;
            }
        }
        else
        {
            if (BUT0 == 1)
            {
                but0_down = 0;
            }
        }
        
        //Check for button 1
        if (but1_down == 0)
        {
            if (BUT1 == 0)
            {
                led_number--;
                led_write(led_number);
                
                but1_down = 1;
            }
        }
        else
        {
            if (BUT1 == 1)
            {
                but1_down = 0;
            }
        }
        
        //Check the milliseconds
        if (millis()>10)
            LED0 = 0;
        else
            LED0 =1;

        
        if(rx_flag==1)
        {
            capture_camera();
            rx_flag=0;
        }
    }
    
}

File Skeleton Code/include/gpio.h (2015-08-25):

/* 
 * File:   gpio.h
 * Author: Kolijn
 *
 * Created on May 31, 2015, 7:58 AM
 */

#ifndef GPIO_H
#define	GPIO_H


#define LED0 LATBbits.LATB13
#define LED1 LATBbits.LATB14
#define LED2 LATFbits.LATF6
#define LED3 LATFbits.LATF4
#define LED4 LATFbits.LATF5
#define LED5 LATBbits.LATB7

#define BUT0 PORTDbits.RD11
#define BUT1 PORTDbits.RD10

#define SERVO_1 PORTEbits.RE5
#define SERVO_2 PORTEbits.RE7



#define SIO_C       PORTGbits.RG2
#define SIO_D       PORTGbits.RG3
//VSyn is an input
#define VSYNC       PORTDbits.RD9
//HRef is an input
///Href and PCLK (Previously OE) are swapped
#define HREF        PORTDbits.RD8
//PCLK is named OE in the spreadsheet
//PCLK (previously OE) and Href are swapped
#define PCLK        PORTGbits.RG9
//XCLK is named RCK in the spreadsheet 
#define XCLK        LATEbits.LATE4 
#define CAM_DATA    PORTD
#define RESET       LATBbits.LATB10
#define PWDN        LATBbits.LATB11

#define MOT1_D1 PORTEbits.RE0
#define MOT1_D2 PORTEbits.RE1
#define MOT1_ENC PORTBbits.RB1
#define MOT2_D1 PORTEbits.RE2
#define MOT2_D2 PORTEbits.RE3
#define MOT2_ENC PORTBbits.RB5

#define SPISS PORTEbits.RE6

void setup_gpio();
void led_write(int num);

#endif

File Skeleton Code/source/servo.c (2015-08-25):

/* 
 * File:   servo.c
 * Author: Kolijn
 *
 * Created on July 20, 2015, 11:13 PM
 */

#include <xc.h>
#include "servo.h"


void setup_pwm();
void set_servo_1(int value);
void set_servo_2(int value);
void set_motor_1(int direction, int speed);
void set_motor_2(int direction, int speed);

/*
 *  Regarding the hardware and the connections
 *
 *      PWM1 is connected to PWM3H/RE5
 *      PWM2 is connected to PWM4H/RE7
 * 
 *      Motor 1 is connected to pins PWM1L and PWM1H
 *      Motor 2 is connected to pins PWM2L and PWM2H
 * 
 * 
 * To run the PWM or the ADC modules the auxiliary clock needs to be configured
 * This clock is derived from the internal RC oscillator. The on-board 10MHz 
 * oscillator as well as the post-pll clock are too fast to use. The internal 
 * RC runs at 7.5 MHZ, and is multiplied by 16 up to 120MHz. In order to run the
 * ADC at max speed the clock is not divided. It is up to the PWM module to 
 * divide the clock further.
 * 
 * 
 *      Servo control
 * 
 * To control a servo, a PWM signal of 20ms (50Hz) has to be sent. A duty cycle
 * of 1ms is the minimum position, and 2ms is the maximum position.
 * 
 * The PWMCON2 divider is set to 64. With the aux clock division of 2 this gives
 * a speed of 1.875 MHz. The Servo must count to 37500. This is still in the 
 * range of the unsigned 16 bit counter.  The min and max values are 1875 and
 * 3750. For a 180 degree servo this should be equal to 0.096 degrees per step. 
 * 
 *      Motor Control
 * The motors are driven at 25 KHz, in order to avoid the audible spectrum. The
 * Motor driver LV8405 supports a maximum of 200KHz. The motor driver has two 
 * inputs, IN1 and IN2 per motor. To drive the motor forwards IN1 needs to be 
 * high with the other input a PWM input. To drive the motor in revers, the 
 * other pin needs to be high with the first pin must be the PWM pin.
 * 
 * To achieve this the override control of the PWM module is used. A single 
 * function sets the the direction and the speed. The ownership of the pins 
 * cannot be set after the PWM is enabled.
 * 
 * The motor uses the same clock as the servo, but with a different period. To
 * drive the motor as 25KHz, the count is set to 75. 
 * 
 *      Errata
 * If the PTCON2 register is not zero, the PWM module may or may not initialize 
 * from an override state. To circumvent this, set the IO Control register 
 * IOCONx via word mode, ie IOCONx = IOCONx & 0xFCFF;
 * This error affects all silicon versions.
 * 
 */



/*
 * Initialize the PWM module for both the Servos and the motors. The motors are 
 * initialized to 25KHz
 */
void setup_pwm()
{     
    PTPER   = 37500;
    
    //Motor1
    IOCON1bits.PENH         = 1;    // PWM controls High pin
    IOCON1bits.PENL         = 1;    // PWM controls Low pin
    IOCON1bits.PMOD         = 0b00;   // Complementary
    IOCON1bits.SWAP         = 0;    // Don't swap pins
    PWMCON1bits.ITB         = 1;    // Use PHASE1 and STPER1 for the timing
    PWMCON1bits.MDCS        = 0;    // PDC1 provides duty cycle
    PHASE1                  = 75;
    
    //Motor2
    IOCON2bits.PENH         = 1;    //PWM controls High pin
    IOCON2bits.PENL         = 1;    //PWM controls Low pin
    IOCON2bits.PMOD         = 0b00; // Complementary
    IOCON2bits.SWAP         = 0;    // Don't swap pins
    PWMCON2bits.ITB         = 1;    //Use PHASE2 and STPER2 for the timing
    PWMCON2bits.MDCS        = 0;    //PDC2 provides the duty cycle.
    PHASE2                  = 75;
    
    //Servo 1
    IOCON3bits.PENH         = 1;    //PWM controls High pin
    IOCON3bits.PMOD         = 0b11; //Independent
    PWMCON3bits.ITB         = 1;    //Use PHASE3 and STPER3 for the timing
    PWMCON3bits.MDCS        = 0;    //PDC3 provides the duty cycle.
    PHASE3 = 37500;
    
    //Servo 2
    IOCON4bits.PENH         = 1;    //PWM controls High pin
    IOCON4bits.PENL         = 0;    //TRIS controls low pin
    IOCON4bits.PMOD         = 0b11; //Independent
    
    
    //Timer output
    IOCON3bits.PENL         = 0;    //PWM controls Low pin
    
    PTCONbits.PTEN          = 1;    //Enable the module
    
    PTCON2bits.PCLKDIV      = 0b011;

    int halfPoint = (MAX_PWM_VALUE-MIN_PWM_VALUE)/2 + MIN_PWM_VALUE;
    set_servo_1(halfPoint);
    set_servo_2(halfPoint);
    set_motor_1(MOT_BRAKE,0);
    set_motor_2(MOT_BRAKE,0);
}


/**
 * Set servo 1 to the specified value. The value has to be between 0 and 1800.
 * If value exceeds this range the maximum or minimum will be set instead. 
 * Servo 2 is connected to PWM3H/RE5
 */
void set_servo_1(int value)
{
    int angle = value + MIN_PWM_VALUE;
    
    //Check that the value is in the acceptable limits
    if (angle < MIN_PWM_VALUE)
    {
        PDC3 = MIN_PWM_VALUE;
        return;
    }    
    
    if (angle > MAX_PWM_VALUE)
    {
        PDC3 = MAX_PWM_VALUE;
        return;
    }
    
    PDC3 = angle;
    return;
}

/**
 * Set servo 2 to the specified value. The value has to be between 0 and 1800.
 * If value exceeds this range the maximum or minimum will be set instead.
 * Servo 2 is connected to PWM4H/RE7
 */
void set_servo_2(int value)
{
    int angle = value + MIN_PWM_VALUE;
    
    //Check that the value is in the acceptable limits
    if (angle < MIN_PWM_VALUE)
    {
        PDC4 = MIN_PWM_VALUE;
        return;
    }    
    
    if (angle > MAX_PWM_VALUE)
    {
        PDC4 = MAX_PWM_VALUE;
        return;
    }
    
    PDC4 = angle;
    return;
}

/*
 * Set the speed and direction of motor 1. Motor 1 is connected to pins PWM1L 
 * and PWM1H. When this function is used the init_motors() function should 
 * already be called. The speed value can be between 0 and 1000
 */
void set_motor_1(int direction, int speed)
{    
    //Take the direction to figure out which 
    int newSpeed = ((speed * 75) / 100);
    
    if (direction == MOT_FORWARDS)
    {
        //This can't be used due to silicon fault
        //IOCON1bits.OVRENH = 1;  //Set the output of the high pin
        //IOCON1bits.OVRENL = 0;  //Pwm on low pin
        //IOCON1bits.OVRDAT = 0b11;
        IOCON1 = (IOCON1 & 0xfc3f)| 0b1011<<6;
        PDC1 = newSpeed;
    }
    if (direction == MOT_REVERSE)
    {
        //This can't be used due to silicon fault
        //IOCON1bits.OVRENH = 0; //PWM on high pin
        //IOCON1bits.OVRENL = 1; //Set the output of the low pin
        //IOCON1bits.OVRDAT = 1;
        IOCON1 = (IOCON1 & 0xfc3f)| 0b0111<<6;
        PDC1 = 75 - newSpeed;
    }
    if (direction == MOT_BRAKE)
    {
        //This can't be used due to silicon fault
        //IOCON1bits.OVRENH = 1;  //Set output for both pins
        //IOCON1bits.OVRENL = 1;
        //IOCON1bits.OVRDAT = 0; //Output should be low
        IOCON1 = (IOCON1 & 0xfc3f)| 0b1100<<6;
        PDC1 =0;
    }
}
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

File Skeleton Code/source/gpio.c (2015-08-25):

#include <xc.h>
#include "gpio.h"

void setup_gpio();
void led_write(int num);

void setup_gpio()
{
    //LED output pins
    TRISBbits.TRISB13   = 0;        //LED0
    TRISBbits.TRISB14   = 0;        //LED1
    TRISFbits.TRISF6    = 0;        //LED2
    TRISFbits.TRISF4    = 0;        //LED3
    TRISFbits.TRISF5    = 0;        //LED4
    TRISBbits.TRISB7    = 0;        //LED5
    
    //Remove Analog input
    //ADPCFG = 0b1111 1110 1010 0010;
    ADPCFG = 0xFeA2;
    
    //Button input pins
    TRISDbits.TRISD11 = 1;
    TRISDbits.TRISD10 = 1;
     
    //VSync is an input
    TRISDbits.TRISD9 = 1;
    //HRef is an input
    TRISGbits.TRISG9 = 1;
    //PCLK is named OE in the datasheet
    TRISDbits.TRISD8 = 1;
    //XCLK is named RCK in the datasheet 
    TRISEbits.TRISE4 = 1; 
    //Camera Data
    TRISD = TRISD | 0xFF;
    //Reset is an output
    PORTBbits.RB10 = 0;
    //PWDN is an output
    PORTBbits.RB11 = 0;    
}

void led_write(int num)
{
    LED5 = (num&0x01);
    LED4 = ((num>>1)&0x01);
    LED3 = ((num>>2)&0x01);
    LED2 = ((num>>3)&0x01);
    LED1 = ((num>>4)&0x01);
    LED0 = 0;
}

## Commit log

2015-03-26 First Commit, most of the circuit layout.
    Ths biggest part of the circuit layout is completed. Minor fixes are still
    required, and some design changes.
    [RoboticsMKII.sch, gpio.sch, mcu.sch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]
2015-03-26 Changed power input to diode and fuse, fixed pinout
    The power input is now protected by a diode and fuse in series.
    The pinout of the PIC is fixed, pin 17 is now RB6 rather than RA6
    [power.sch]
2015-03-28 Added initial footprint associations, caps and resistors.
    Kicad is giving weird errors for the libraries and BOM generator.
    The libraries have to be downloaded manually from github, and
    then added.
    [RoboticsMKII.sch, gpio.sch, mcu.sch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]
2015-03-30 Added diodes to motor driver
    [RoboticsMKII_BOM.csv, gpio.sch, mcu.sch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]
2015-03-30 Added crystal footprint
    [RoboticsMKII.kicad_pcb, gpio.sch, mcu.sch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]
2015-03-31 Finished the footprint allocation, started on the PCB layout.-s
    [RoboticsMKII.sch, gpio.sch, mcu.sch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]
2015-04-02 Added UART, Gnd and 3.3v pins
    [gpio.sch, mcu.sch]
2015-04-02 PCB is now 10cmx5cm, some components moved around for more space
    [RoboticsMKII.kicad_pcb, gpio.sch, mcu.sch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]
2015-04-05 Removed connection between data_4 and data_5
    [RoboticsMKII.kicad_pcb, mcu.sch]
2015-04-05 Motor Diodes done, some of the power connections
    [RoboticsMKII.kicad_pcb, RoboticsMKII.sch, mcu.sch]
2015-04-05 More power layout, improved feedback diodes. All fonts now the same
    [RoboticsMKII.kicad_pcb]
2015-04-05 Bus routing done. No idea what to do with the MCU oscillator.
    [RoboticsMKII.kicad_pcb]
2015-04-06 Removed bus, rotated mcu to fit crystal in
    [RoboticsMKII.kicad_pcb]
2015-04-06 Most of the Camera bus routed, analog bus routed as well. ICSP and SPI are next
    [RoboticsMKII.kicad_pcb]
2015-04-06 Most signals are done now, only power remains. This will definitely be a 4 layer board
    [RoboticsMKII.kicad_pcb]
2015-04-06 Done with the power layout.
    [RoboticsMKII.kicad_pcb]
2015-04-06 Added an additional cap for the MCU, added copper fill on all layers.
    [RoboticsMKII.kicad_pcb, power.sch]
2015-04-06 Added OSHW logo on the back and front text. Filled copper and generated gerbers.
    [RoboticsMKII-B_Cu.gbl, RoboticsMKII-B_Mask.gbs, RoboticsMKII-B_SilkS.gbo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]
2015-04-15 Added caps next to motor feedback diodes
    [RoboticsMKII-B_Cu.gbl, RoboticsMKII-B_Mask.gbs, RoboticsMKII-B_SilkS.gbo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]
2015-04-19 Did some fixes, added better footprint for the flyback diodes:
    Re-routed camera bus so that there is more ground for the crystal.
    Added ground pour keepouts under the MCU.
    Changed the footprint for the motor flyback diodes.
    Changed the camera module to have 24 pins, 2 won't be connected
    Checked the footprints for dsPIC, MCP and LV8045
    Increased thermal pad for voltage regulator
    [RoboticsMKII.kicad_pcb, gpio.sch, motors.sch]
2015-04-19 More Changes:
    Checked top and bottom silkscreen - almost no overlaps with pads or holes
    Added Robotic club logo to board, generated from png file.
    Modified on-board text.
    [RoboticsMKII.kicad_pcb]
2015-04-20 Moved all fabrication layer to silkscreen
    Moved tracks to look better with copper pour
    Fixed more silscreen-on-via errors
    [RoboticsMKII.kicad_pcb]
2015-04-20 Fixed some DRC issues, connected ground traces
    No more unccenected pads now
    [RoboticsMKII-B_Cu.gbl, RoboticsMKII-B_Mask.gbs, RoboticsMKII-B_SilkS.gbo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]
2015-04-20 Added keepout under some components
    [RoboticsMKII.kicad_pcb]
2015-04-21 Some small changes
    [RoboticsMKII-B_Cu.gbl, RoboticsMKII-B_Mask.gbs, RoboticsMKII-B_SilkS.gbo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]
2015-04-23 Increased pad sizes for easy soldering, final commit before ordering
    [RoboticsMKII-B_Cu.gbr, RoboticsMKII-B_Mask.gbr, RoboticsMKII-B_Mask.gbs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]
2015-05-05 Some changes?
    [RoboticsMKII-B_Cu.gbl, RoboticsMKII-B_Cu.gbr, RoboticsMKII-B_Mask.gbr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]
2015-05-05 Started 2 layer layout
    [RoboticsMKII.kicad_pcb]
2015-05-05 Many buslines done, camera bus almost there, LED bus almost done, analog bus almost. SPI and pwm needs attention
    [RoboticsMKII.kicad_pcb]
2015-05-05 More done. PWM and SPI need attention
    [RoboticsMKII.kicad_pcb]
2015-05-06 Finished 2-layer routing, now it needs to be checked
    [RoboticsMKII.kicad_pcb]
2015-05-06 2layers almost done. Silkscreen needs checking
    [RoboticsMKII-B_Cu.gbl, RoboticsMKII-B_Mask.gbs, RoboticsMKII-B_SilkS.gbo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]
2015-05-06 Top Silkscreen fixed. Almost done
    [RoboticsMKII-B_Cu.gbl, RoboticsMKII-B_Mask.gbs, RoboticsMKII-B_SilkS.gbo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]
2015-05-07 Changed all via sizes, changed layout, changed jack footprint to original
    [RoboticsMKII-B_Cu.gbl, RoboticsMKII-B_Mask.gbs, RoboticsMKII-B_SilkS.gbo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]
2015-05-08 Final version
    [RoboticsMKII-B_Cu.gbl, RoboticsMKII-B_Mask.gbs, RoboticsMKII-B_SilkS.gbo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]
2015-08-07 Added the camera adapter-s
    [CameraAdaptor.kicad_pcb, CameraAdaptor.sch]
2015-08-11 Did the basic layout, avaiting via size, track width specifications.
    [CameraAdaptor.kicad_pcb, CameraAdaptor.sch]
2015-08-14 Changed CamerAdaptor layout, changed track thickness
    [CameraAdaptor.kicad_pcb, CameraAdaptor.sch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]
2015-08-19 Removed pdf outputs, added correct gerber files
    One of the gerber files doesn't register correct with
    the cnc machine: The hole should be positioned at 80,100
    but ends at 800,100
    [CameraAdaptor.kicad_pcb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]
2015-08-20 Fixed bootloader, added link, fixed skeleton code
    [main.c, timer.c]
2015-08-21 Fixed camera board
    [CameraAdaptor.kicad_pcb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]
